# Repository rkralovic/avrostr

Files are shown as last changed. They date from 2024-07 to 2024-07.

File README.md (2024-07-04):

# AVR-OSTR

This project is an implementation of a turtle robot based on AVR microcontroller.

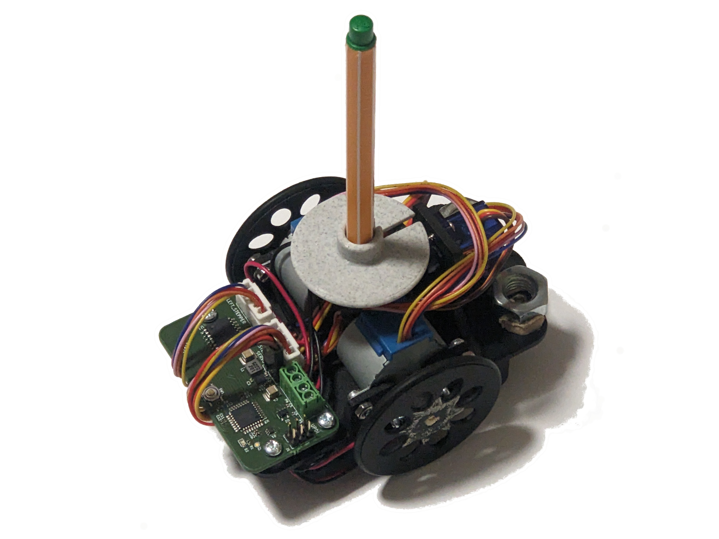
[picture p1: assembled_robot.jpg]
assembled robot


## Mechanical design

The hardware design is based on [https://www.instructables.com/OSTR/](https://www.instructables.com/OSTR/).

Mechanical parts are designed using [OpenSCAD](https://openscad.org). Running
`make` in the `mechanical` directory builds STL files suitable for 3d-printing.
The design has the following parts:

* `Chassis.scad` is the main chassis structure.
* `Caster.scad` holds a support bearing ball.
* `PenCollar.scad` holds the pen.
* `Wheel.scad` is the wheel. You need to print 2 of them

The following extra parts are needed for assembly:

* Bearing ball with diameter approx 15.875mm.
* 2x o-ring 42mm x 3mm used as tires. It is important that it fits tightly to the wheels.
* 2x battery holder for 2 AA batteries (e.g. 12BHC321A-GR).
* M3 nuts and screws (for battery holders and stepper motors).
* DIN7981 screws to fix the wheels and PCB
  ([example](https://www.conrad.ch/de/p/toolcraft-din7981-c-h-2-9c4-5-linsenblechschrauben-2-9-mm-4-5-mm-kreuzschlitz-phillips-din-7981-stahl-verzinkt-1-st-889176.html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)).
* (optional) Two large nuts that can be glued to the back of the chassis for better stability.

## Electronic design

Schematics and PCB layout are provided as a Kicad project in this directory.
Component list is summarized in `bom.csv`.

## Firmware

Source of the firmware, which runs on the AVR microcontroller of the robot, is
in the directory `fw`. You need reasonable new avr-g++ in order to compile the
firmware, which uses C++20. Development was done using avr-g++ 11.2.0.

The AVR firmware can be flashed using avrdude and an UPDI-capable programmer by
running `make write`.

A smoke test is in `fw/test`. It uses simavr library to simulate the AVR code.

Note: To compile the firmware, you need to first generate the input data, see
the next section for details. Beyond that, the tests depend on simavr, gmock,
and gtest libraries.

## Image data

The image data for the robot are prepared using a tool in `gendata` directory.
Source images are in `gendata/input` in svg file format. The tool depend on
absl, cairo, xcb, cairo-pdf, and xcb-iccm libraries.

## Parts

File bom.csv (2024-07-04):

Part number | Quantity | Designators | Footprint | Value
81-GRM155R61A106ME1D | 2 | C1,C3 | Capacitor_SMD:C_0402_1005Metric | 10u
81-GRM32ER61A107ME0K | 2 | C2,C4 | riso:C_1210_3225Metric | 100u
81-GRM155R61H105ME5D | 5 | C5,C6,C7,C9,C11 | Capacitor_SMD:C_0402_1005Metric | 1u
81-GRM155R71H104KE4D | 4 | C8,C10,C12,C14 | Capacitor_SMD:C_0402_1005Metric | 100n
GCM188R71H224KA64 | 1 | C13 | Capacitor_SMD:C_0603_1608Metric | 220n
241-BAT54BRWR100001 | 1 | D1 | Package_TO_SOT_SMD:SOT-363_SC-70-6 | BAT54BRW
710-150060RS75000 | 2 | D2,D3 | LED_SMD:LED_0603_1608Metric | RED
649-78511-203HLF | 1 | J1 | Connector_PinHeader_2.54mm:PinHeader_2x03_P2.54mm_Vertical | UPDI
XFL4020-102MEC | 1 | L1 | Inductor_SMD:L_Coilcraft_XxL4020 | 1u
651-1984617 | 2 | P5,P6 | TerminalBlock_Phoenix:TerminalBlock_Phoenix_PT-1,5-2-3.5-H_1x02_P3.50mm_Horizontal | BATT1
538-22-28-9034 | 1 | P7 | library:Pin_Header_Straight_1x03 | SERVO
603-RC0402FR-13510RL | 2 | R1,R3 | Resistor_SMD:R_0402_1005Metric | 510
603-AC0402FR-071KL | 1 | R2 | Resistor_SMD:R_0402_1005Metric | 1K
RC0402FR-07604KL | 1 | R4 | Resistor_SMD:R_0402_1005Metric | 600k
791-WR04X1003FTL | 1 | R6 | Resistor_SMD:R_0402_1005Metric | 100k
611-PTS526SM15SMTR2L | 1 | SW1 | riso:SW4-SMD-5.2X5.2X1.5MM | SMD-BUTTON_4P-5.2X5.2X1.5MM-SKQGADE010_
757-TCR1HF33BLMCT | 1 | U2 | Package_TO_SOT_SMD:SOT-23-5 | TCR1HF33
494-AVR64DD32-I/PT | 1 | U3 | Package_QFP:TQFP-32_7x7mm_P0.8mm | AVR64DD32-I/PT
595-TPS630702RNMR | 1 | U4 | riso:VQFN-15-TPS63070 | TPS63070
932-MIKROE-1530 | 2 | P3,P4 | library:JST_B5B-XH-A | LEFT_STEPPER
12BHC321A-GR | 2 | P5,P6 | TerminalBlock_Phoenix:TerminalBlock_Phoenix_PT-1,5-2-3.5-H_1x02_P3.50mm_Horizontal | BATT1
485-169 | 1 | P7 | library:Pin_Header_Straight_1x03 | SERVO
4518-ULN2803ACT-ND | 1 | U1 | Package_SO:SOP-18_7x12.5mm_P1.27mm | ULN2803

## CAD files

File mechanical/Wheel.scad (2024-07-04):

wheelDiameter = 47.5;  // not including the gasket
gasketDiameter = 3;
innerWidth = 2.0;
outerWidth = max(gasketDiameter + 1, innerWidth);

hubDiameter = 11.5;
hubHeight = 9;
hubRounding = 1;
hubCutWidth = 3.25;

// spokeDiameter = (wheelDiameter / 2 - 6.5) - 9;
spokeDiameter = ((wheelDiameter - hubDiameter) / 2 - hubRounding - outerWidth) * 0.85;
spokeAspectRatio = 0.75;
numSpokes = 8;

// pilot hole for M3 self-tapping screw in hub 
drillHoleDiameter1 = 2.5;
drillHoleDiameter2 = 2.5;

$fa = 3;
$fs = 0.3;
//$fn = 20;

module toroid(r1, r2) {
  rotate_extrude()
    translate([r2, 0, 0]) circle(r = r1);
}

module simpleCylinder(h, r) {
  cylinder(h, r, r, center = false);
}

module basicWheel() {
  difference() {
    simpleCylinder(outerWidth, wheelDiameter / 2);
    translate([0, 0, outerWidth / 2])
      toroid(gasketDiameter / 2, wheelDiameter / 2);

    minkowski() {
      translate([0, 0, outerWidth])
        simpleCylinder(outerWidth, wheelDiameter / 2 - outerWidth);
      sphere(outerWidth - innerWidth);
    }
  }
}

module spoke() {
  scale([1, spokeAspectRatio, 1])
  difference() {
    simpleCylinder(innerWidth + 1, spokeDiameter / 2);
    translate([0, 0, innerWidth / 2])
      toroid(innerWidth / 2, spokeDiameter / 2);
  }
}

module hub() {
  union() {
    minkowski() {
      translate([0, 0, hubRounding])
        simpleCylinder(hubHeight - 2 * hubRounding, (hubDiameter / 2) - hubRounding);
      sphere(hubRounding);
    };

    // bottom rounding
    difference() {
      translate([0, 0, innerWidth])
        simpleCylinder(hubRounding, hubDiameter / 2 + hubRounding);
      translate([0, 0, innerWidth + hubRounding])
        toroid(hubRounding, hubDiameter / 2 + hubRounding);
    }
  }
}

module Wheel() {
  union() {
    difference() {
      union() {
        basicWheel();
        hub();
      }

      // Drill spokes
      for (i = [0:numSpokes])
        rotate( i * 360 / numSpokes, [0, 0, 1])
          translate([-(hubDiameter / 2 + hubRounding + wheelDiameter / 2 - outerWidth) / 2, 0, 0])
            spoke();

      // Drill axis
      translate([0, 0, -1])
        intersection() {
          R = 2.75;
          simpleCylinder(hubHeight + 2, R);
          cube([hubCutWidth, 2 * R, 2 * hubHeight + 3], center = true);
        };

      // Drill Screw hole
      #for (i = [-1, 1])
        translate([i * (hubDiameter / 4 + hubCutWidth /4), 0, 6]) 
        rotate([0, 90, 0])
        rotate([90*(i + 1), 0, 0])
          cylinder((hubDiameter - hubCutWidth)/ 2 + 0.01, drillHoleDiameter1 / 2, drillHoleDiameter2 / 2, center = true);
    }
    // screw
    %translate([1.62, 0, 6]) rotate([0, 90, 0])
    union() {
      screwHeight = 4.8; // 4.5 is better, but ~6 is what I have and acceptable, too
      cylinder(h = screwHeight, d = 2.9);
      difference() {
        translate([0, 0, screwHeight])
          sphere(d = 5.6);
        translate([0, 0, screwHeight/2])
          cube([6, 6, screwHeight], center=true);
      }
    }
  }
}

Wheel();

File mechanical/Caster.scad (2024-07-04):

// Original: http://www.thingiverse.com/thing:8959/
// Marble Caster by HipsterLogic
// License: https://creativecommons.org/licenses/by-sa/3.0/

// Modified by 648.ken@gmail.com
// MakersBox.blogspot.com

// Added tapper the top lip to keep it from snagging on things.
// Added recess for screw heads if baseThickness > 3mm
// Added pedistal base so you can adjust platform hieght.

// Modified by Richard Kralovic

deckHeight = 18.5;    // from chassis bottom to ground, (must be at lease ballDiameter)
ballDiameter = 15.875;    // 7/16" ball bearing = 12.25mm, WAS 16.5  16mm = 5/8" ball bearing
ballTolerance = 0.25 + 0.25;  // play between ball and surface
wallThickness = 2.5;  // was 2.5
gapWidth = ballDiameter / 3;
baseThickness = 2.5; // was 3

pedistalWidth = ballDiameter + wallThickness * 2 + ballTolerance * 2;

baseWidth = 30; // distance between mounting holes

M3holeDia = 3.5;
M3nutDia = 6.5;

baseHeight = deckHeight - ballDiameter / 2 + ballTolerance;

module mainShape() {
  // mounting cross-piece
  translate([-baseWidth/2, -wallThickness - M3holeDia / 2, 0]) 
    cube([baseWidth, wallThickness * 2 + M3holeDia, baseThickness]);

  // bolt ends
  translate([baseWidth / 2, 0, 0]) 
    cylinder(baseThickness, M3holeDia / 2 + wallThickness, M3holeDia / 2 + wallThickness, $fn=40);
  translate([-baseWidth / 2, 0, 0]) 
    cylinder(baseThickness, M3holeDia / 2 + wallThickness, M3holeDia / 2 + wallThickness, $fn=40);


  // main cylindrical body
  translate([0, 0, 0])
    cylinder(baseHeight, pedistalWidth / 2, pedistalWidth / 2, $fn=90);

  difference(){
    // tapper shere at top
    translate([0, 0, baseHeight])
      sphere(r = pedistalWidth / 2, $fn=90);

    // shave the top flat
    R = ballDiameter / 2;
    insertRestraint = 0.5;        
    shaveHeight = sqrt((R+ballTolerance)^2 - (R - insertRestraint)^2);
    echo(shaveHeight);
    translate([0, 0, baseHeight + shaveHeight])
      cylinder(25, 25, 25, $fn=90);
  }
}

module cutout() {
  // ball hole
  translate([0, 0, baseHeight]) 
    sphere(ballDiameter / 2 + ballTolerance, $fn=90);
      
  for (r = [0:90:90]) rotate([0, 0, 45 + r]) {
    // slot to remove ball
    slotOffset = ballDiameter / 2.5;  // distance below baseHeight to cut slot
    if (baseHeight - slotOffset > baseThickness) {
      translate([-gapWidth / 2, -baseWidth / 2, baseHeight - slotOffset]) 
        cube([gapWidth, baseWidth, ballDiameter]);
    } else { // don't cut into base
      translate([-gapWidth / 2, -baseWidth / 2, baseThickness]) 
       cube([gapWidth, baseWidth, ballDiameter]);        
    }
  }
}

module mountingHoles(){
  // m3 holes
  for (i = [-1, 1]) translate([ i * baseWidth / 2, 0, -1])
    cylinder(baseThickness + 2, M3holeDia / 2, M3holeDia / 2, $fn=30);
}

module Caster() {
  rotate([0, 0, 90])
  difference() {
    mainShape();
    cutout();
    mountingHoles();
  }

  // show ball
  %translate([0, 0, baseHeight - ballTolerance]) 
    sphere(ballDiameter / 2, $fn=50);
}

Caster();

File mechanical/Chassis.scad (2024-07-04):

//$fa = 3;
//$fs = 0.3;
$fn = 50;

// Wheel diameter: 47.5 + 3 (gasket, see Wheel.scad) = 50.5
// Distance ground - shaft = 25.25
// Distance ground - bottom of chassis (Caster.scad) = 18.5
// Distance bottom of chassis - shaft = 6.75

wallThickness = 2.5;

baseThickness = wallThickness;
shaftPosition = 6.75;

module roundedCubeXYZR(xdim ,ydim ,zdim, rdim){
  hull() { // https://youtu.be/gKOkJWiTgAY
    translate([rdim, rdim, 0]) cylinder(zdim, rdim, rdim);
    translate([xdim-rdim, rdim, 0]) cylinder(zdim, rdim, rdim);
    translate([rdim, ydim-rdim, 0]) cylinder(zdim, rdim, rdim);
    translate([xdim-rdim, ydim-rdim, 0]) cylinder(zdim, rdim, rdim);
  }
}

// Interface more compatible with cube()
module roundedCube(dims, radius=2, center=false) {
  xdim = dims[0];
  ydim = dims[1];
  zdim = dims[2];
  if (center) {
    translate([-xdim  / 2, -ydim / 2, -zdim / 2])
      roundedCubeXYZR(xdim, ydim, zdim, radius);
  } else {
    roundedCubeXYZR(xdim, ydim, zdim, radius);
  }
}

module ellipsoidFillet(dims, h0, full = true) {
  module ell() {
    translate([0, 0, dims[2] / 2]) scale([1, 1, 2 * (dims[2] - h0) / dims[0]]) rotate([90, 0, 0])
      cylinder(h = dims[1] + 0.1, d = dims[0], center = true);
  }
  translate([0, 0, dims[2] / 2])
  difference() {
    cube(dims, center = true);
    if (full) {
      ell();
    } else {
      translate([-dims[0] / 2, 0, 0]) scale([2, 1, 1]) ell();
    }
  }
}

M3holeDia = 3.6;
M3nutDia = 6.5;

stepperBlockH = 17;  // distance from center to the top of the rectangular block
stepperBlockW = 14.6;
stepperBulkThickness = wallThickness + 1;

stepperShaftRadius = 5;
stepperShaftOffset = 8;
stepperDiameter = 28;
stepperTabWidth = 7;
stepperTolerance = 0.6;
module Stepper() {
  thickness = 3;

  tol= stepperTolerance;

  h1 = 19;  // body thickness, minimum 19
  h2 = 10;  // arbitrary, to have long enough drill holes
  blockH = stepperBlockH;
  blockW = stepperBlockW;
  d = stepperDiameter;
  screw_distance = 35;
  tab_width = stepperTabWidth;
  shaft_offset = stepperShaftOffset;
  shaft_radius = stepperShaftRadius;

  union() {
    rotate(-90, [0, 0, 1])
    rotate(90, [1, 0, 0])
    translate([0, shaft_offset, - h1 / 2 - tol]) {
      cylinder(h = h1 + 2 * tol, r = d / 2 + tol, center=true);  // stepper body

      for (i = [-1, 1])
        translate([i * screw_distance / 2, 0, 0]) {
          translate([0, 0, -thickness +h1 / 2 - tol])
          cylinder(h = thickness + 2*tol, r = tab_width / 2 + tol, center=false);
          translate([0, 0, -thickness +h1/2])
            cylinder(h = thickness + h2, d = M3holeDia, center=false);
        }

      translate([0, 0, h1 / 2 + tol - thickness / 2])
        cube([screw_distance, tab_width + 2*tol, thickness], center=true);

      // Not part of the motor body, but useful to keep too thin areas left
      translate([0, d/4, -thickness /2 + h1/2])
      cube([screw_distance + tab_width + 2*tol, d / 2, thickness + 2 * tol], center=true);

      // Shaft
      translate([0, -shaft_offset, h2 / 2])
        cylinder(h = h1 + h2, r = shaft_radius + tol, center=true);

        translate([0, blockH / 2, 0])
          cube([blockW + 2 * tol, blockH + 2 * tol, h1 + 2 * tol], center=true);

    }

    // Not part of the motor body, but useful to keep too thin areas left
    cutout = d * 0.25;
    translate([0, -cutout / 2, shaft_offset - d/2 - baseThickness])
      cube([h1 + 2*tol, cutout, d + 2*tol ]);
  }
}

stepperBulkW = 43;
stepperBulkH = stepperShaftOffset + shaftPosition + stepperTabWidth / 2;//19.5

module StepperBulk() {
  bulkW = stepperBulkW;
  bulkH = stepperBulkH;
  r = 2;
  bulkThickness = stepperBulkThickness;

  union() {
    translate([-(bulkW) / 2, 0, 0])
      rotate([90, 0, 0])
        union() {
          cube([bulkW, shaftPosition, bulkThickness]);
          for (i = [0, 2])
            translate([i * (bulkW / 2 + stepperShaftRadius + stepperTolerance) / 2, 0, 0])
              roundedCube([bulkW / 2 - stepperShaftRadius - stepperTolerance, bulkH, bulkThickness], r);
        }

      r2 = 5;
      translate([0, -r2/2 - bulkThickness, r2/2 + baseThickness ])
      difference() {
        filletW = bulkW - 2 * r2;
        union () {
          cube([filletW, r2, r2], center=true);
          for (i = [-1, 1])
          translate([i * filletW / 2, r2/2, -r2/2])
          intersection() {
            sphere(r2);
            translate([(i - 1) / 2 *r2, -r2, 0]) cube([r2, r2, r2]);
          }
        }
        translate([0, -r2/2, r2/2]) rotate([0, 90, 0])
          cylinder(h = 2*r2 + filletW + 0.1, r = r2, center = true);
      }
  }
}

railWidth = 2.9;
railOffset = 5.8;

penDiameter = 8.8;  // Including tolerance. Maximum 9.
// Stabilo pen has 8.4mm diameter, 0.5mm tolerance
barrelDiameter = penDiameter + 2 * wallThickness;
barrelHeight = 33;  // 26

// servo bracket variables
servoOverallHeight = 34.5;  // 34.5
servoBodyHeight = 24;
servoBodyWidth = 13;
servoScrewDia = 1.5;
servoScrewOffset = 2;
servoFwdOffset = penDiameter / 2 + wallThickness + 19;   // was 14.5
servoSideOffset = 3;
servoVerticalOffset = 8;  // distance between top of holder and servo body center, was 5

batteryOffset = 20.5;
batteryShift = 0;  // -2 is needed in the original position of servo
batteryScrewDistance = 15;

module HolderBulk() {
  baseWid = 19;
  baseLen = railWidth + 2 * railOffset;
  cornerRounding = 2;

  // pen holder
  translate([0, 0, baseThickness])
  cube([baseWid, baseLen, 2 * baseThickness], center = true);

  translate([0, 0, baseThickness])
    cylinder(barrelHeight - wallThickness / 2, r1 = baseLen / 2, r2 = barrelDiameter / 2);
  translate([0, 0, baseThickness + barrelHeight - wallThickness / 2])
    toroid(wallThickness / 2, (barrelDiameter - wallThickness) / 2);

  union() {
    bracketThickness = baseThickness + 0.5;
    bracketWidth = servoBodyWidth + 4 * baseThickness;
    // servo bracket
    rotate([0, 0, 180])
    translate([-servoFwdOffset, servoSideOffset, barrelHeight - servoVerticalOffset])
    rotate([90, 0, 90])
    union() {
      difference() {
        // base
        translate([ 0, -(barrelHeight - servoVerticalOffset - servoOverallHeight / 2) / 2, bracketThickness / 2 ])
            roundedCube([bracketWidth, servoOverallHeight / 2 + barrelHeight - servoVerticalOffset,
                         bracketThickness], cornerRounding, center = true);

        // body cutout
        translate([ 0, 0, bracketThickness / 2])
            cube([servoBodyWidth, servoBodyHeight, bracketThickness + 0.5], center = true);

        // vertical screw holes
        translate([ -0.1, -servoBodyHeight / 2 - servoScrewOffset, -0.1 ])
            cylinder(bracketThickness + 0.2, servoScrewDia / 2, servoScrewDia / 2);
        translate([ 0, servoBodyHeight / 2 + servoScrewOffset, -0.10 ])
            cylinder(bracketThickness + 0.2, servoScrewDia / 2, servoScrewDia / 2);

        // space for inserting m3 nut below
        shift = bracketThickness / 2;
        translate([-servoSideOffset, -0.1 + 1 + 2.5 + 1.5 - baseThickness / 2 - barrelHeight + servoVerticalOffset, shift])
          intersection() {
            roundedCube([5.7, 1 + 2.5 + 1.5 + baseThickness, bracketThickness + 0.1], radius = 1, center = true);
            // Ugly - we need to place the nut to the correct hole
            translate([0, 0, servoFwdOffset - shift - batteryOffset - batteryScrewDistance / 2]) rotate([90, 30, 0])
              cylinder(1 + 2*(baseThickness + 5), d = M3nutDia, center = true, $fn=6);
          }
      }

      // Servo body for checking
      %union() {
        mountOffset = 16 + 2.45;  // TODO: measure - 16 by datasheet, but that's probably not counting the thicnkess of the tab
        translate([0, 0, 26.9 / 2 - mountOffset])
          cube([12.6, 22.8, 26.9], center = true);
        translate([0, 22.8/4, 26.9 - mountOffset]) rotate([0, 0, 90])
          cylinder(h = 32.2 - 26.9, d = 7.3);
//        mountOffset = 16 + 2.45;  // TODO: measure - 16 by datasheet, but that's probably not counting the thicnkess of the tab
//        translate([0, 0, 26.7 / 2 - mountOffset])
//          cube([12.6, 22.8, 26.7], center = true);
//        translate([0, 22.8/4, 26.7 - mountOffset]) rotate([0, 0, 90])
//          cylinder(h = 34.5 - 26.7, d = 7);
      }
    }
    // fillets
    {
      w = chassisW / 2 - servoSideOffset - bracketWidth / 2 - stepperBulkThickness;
      translate([servoFwdOffset - bracketThickness / 2, w / 2 - chassisW / 2 + stepperBulkThickness, baseThickness])
      rotate([0, 0, 90]) 
        ellipsoidFillet([w + 0.01, bracketThickness, stepperBulkH], stepperBulkH / 3, false);
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

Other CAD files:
mechanical/PenCollar.scad

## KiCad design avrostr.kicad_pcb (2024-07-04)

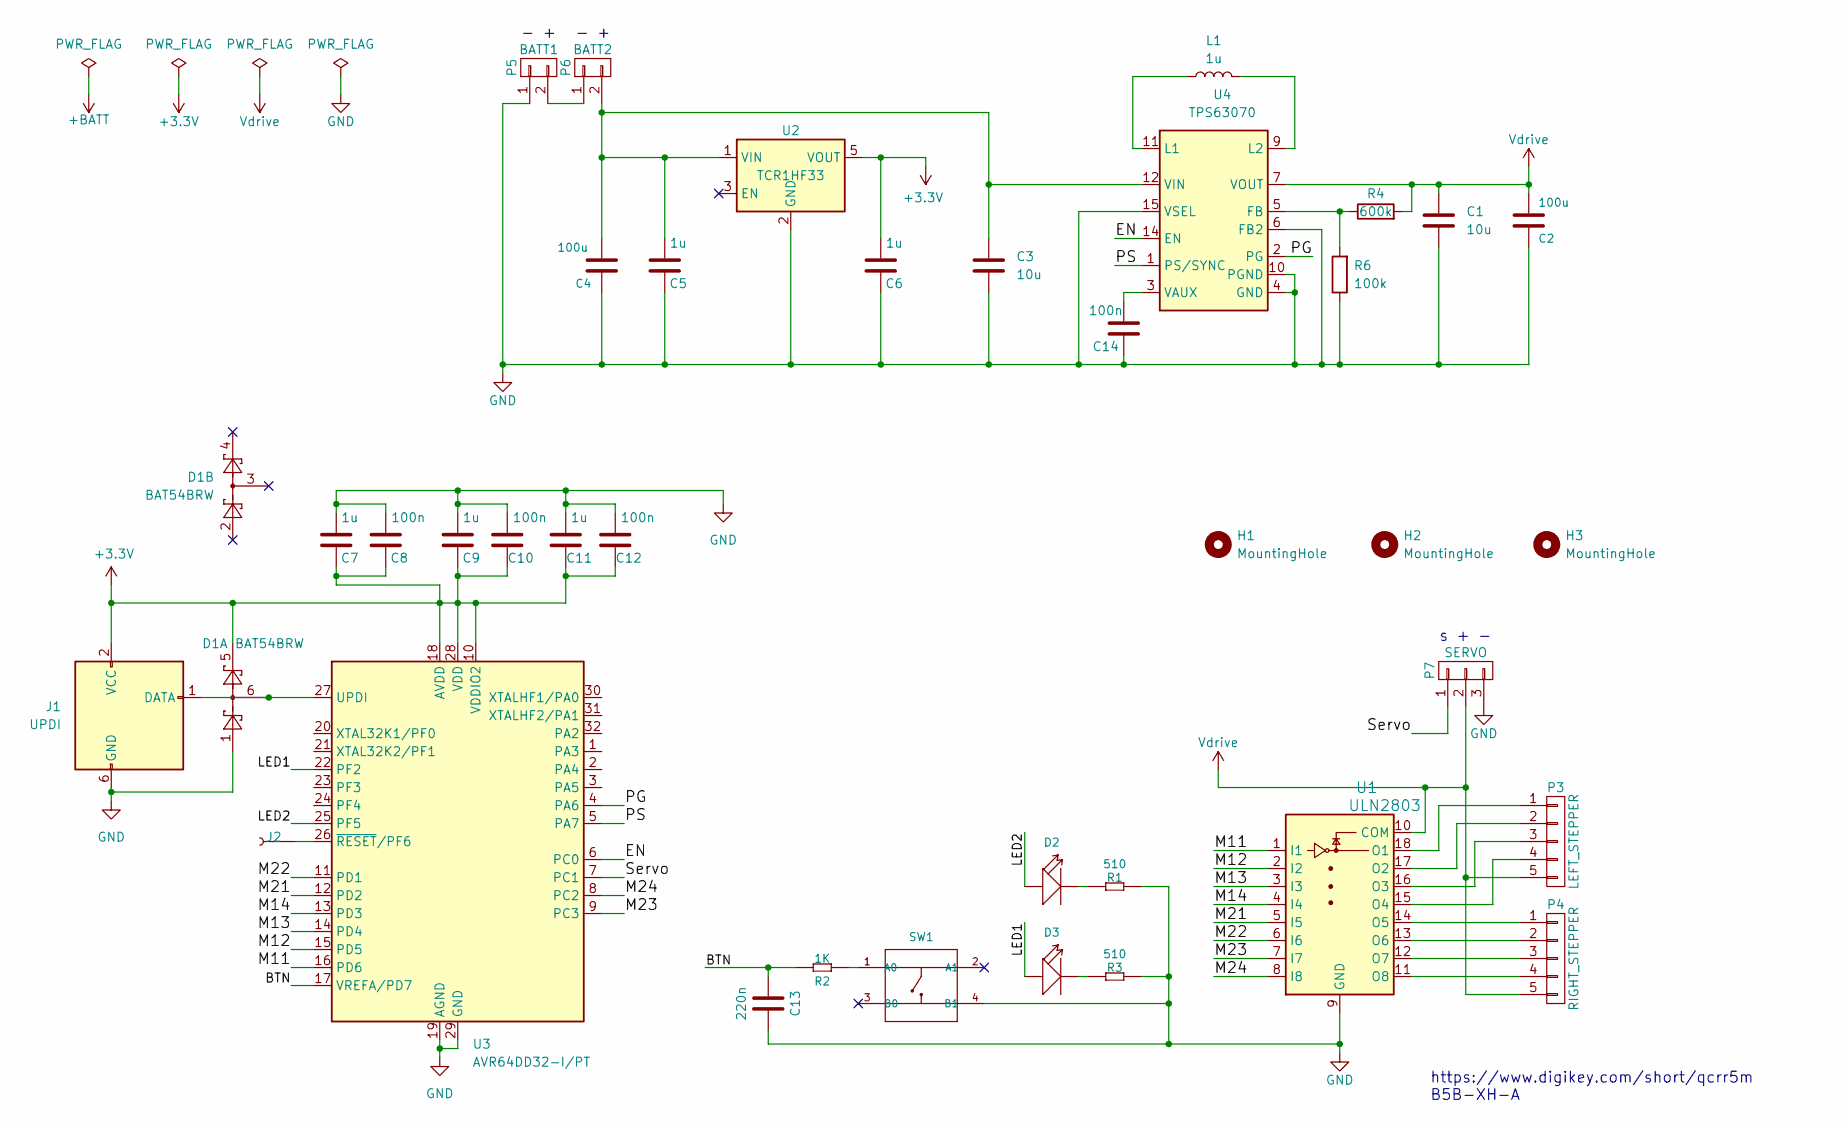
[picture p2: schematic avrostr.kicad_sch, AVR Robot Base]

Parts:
C1, C3: 10u; C_0402_1005Metric; Mouser 81-GRM155R61A106ME1D
C2, C4: 100u; C_1210_3225Metric; Mouser 81-GRM32ER61A107ME0K
C5, C6, C7, C9, C11: 1u; C_0402_1005Metric; Mouser 81-GRM155R61H105ME5D
C8, C10, C12, C14: 100n; C_0402_1005Metric; Mouser 81-GRM155R71H104KE4D
C13: 220n; C_0603_1608Metric; Mouser GCM188R71H224KA64
D1: BAT54BRW; SOT-363_SC-70-6; Mouser 241-BAT54BRWR100001
D2, D3: RED; LED_0603_1608Metric; Mouser 710-150060RS75000
H1, H2, H3: MountingHole; MountingHole_3.2mm_M3_ISO14580
J1: UPDI; PinHeader_2x03_P2.54mm_Vertical; Mouser 649-78511-203HLF
J2: Conn_01x01_Female; TestPoint_Pad_D1.0mm
L1: 1u; L_Coilcraft_XxL4020; Mouser XFL4020-102MEC
P3: LEFT_STEPPER; JST_B5B-XH-A; Digikey 455-2270-ND
P4: RIGHT_STEPPER; JST_B5B-XH-A; Digikey 455-2270-ND
P5: BATT1; TerminalBlock_Phoenix_PT-1,5-2-3.5-H_1x02_P3.50mm_Horizontal; Mouser 651-1984617
P6: BATT2; TerminalBlock_Phoenix_PT-1,5-2-3.5-H_1x02_P3.50mm_Horizontal; Mouser 651-1984617
P7: SERVO; Pin_Header_Straight_1x03; Digikey 1849-1003-ND
R1, R3: 510; R_0402_1005Metric; Mouser 603-RC0402FR-13510RL
R2: 1K; R_0402_1005Metric; Mouser 603-AC0402FR-071KL
R4: 600k; R_0402_1005Metric; Mouser RC0402FR-07604KL
R6: 100k; R_0402_1005Metric; Mouser 791-WR04X1003FTL
SW1: type="R" model="SMD-BUTTON_4P-5.2X5.2X1.5MM-SKQGA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; SW4-SMD-5.2X5.2X1.5MM; MPN SKQGADE010; LCSC C318889
U1: ULN2803; SOP-18_7x12.5mm_P1.27mm; Digikey 4518-ULN2803ACT-ND
U2: TCR1HF33; SOT-23-5; Mouser 757-TCR1HF33BLMCT
U3: AVR64DD32-I/PT; TQFP-32_7x7mm_P0.8mm; Digikey 150-AVR64DD32-I/PT-ND
U4: TPS63070; VQFN-15-TPS63070; Mouser 595-TPS630702RNMR

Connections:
+3.3V: C6.2, C7.1, C8.2, C9.1, C10.2, C11.1, C12.2, D1.5, J1.2 (VCC), U2.5 (VOUT), U3.10 (VDDIO2), U3.18 (AVDD), U3.28 (VDD)
/BTN: C13.1, R2.1, U3.17 (VREFA/PD7)
/EN: U3.6 (PC0), U4.14 (EN)
/LED1: D3.1 (+), U3.22 (PF2)
/LED2: D2.1 (+), U3.25 (PF5)
/M11: U1.1 (I1), U3.16 (PD6)
/M12: U1.2 (I2), U3.15 (PD5)
/M13: U1.3 (I3), U3.14 (PD4)
/M14: U1.4 (I4), U3.13 (PD3)
/M21: U1.5 (I5), U3.12 (PD2)
/M22: U1.6 (I6), U3.11 (PD1)
/M23: U1.7 (I7), U3.9 (PC3)
/M24: U1.8 (I8), U3.8 (PC2)
/PG: U3.4 (PA6), U4.2 (PG)
/PS: U3.5 (PA7), U4.1 (PS/SYNC)
/Servo: P7.1, U3.7 (PC1)
GND: C1.2, C2.2, C3.2, C4.2, C5.1, C6.1, C7.2, C8.1, C9.2, C10.1, C11.2, C12.1, C13.2, C14.2, D1.1, J1.6 (GND), P5.1, P7.3, R1.2, R3.2, R6.1, SW1.4 (B1), U1.9 (GND), U2.2 (GND), U3.19 (AGND), U3.29 (GND), U4.4 (GND), U4.6 (FB2), U4.10 (PGND), U4.15 (VSEL)
unnamed: C14.1, U4.3 (VAUX)
unnamed: D1.6, J1.1 (DATA), U3.27 (UPDI)
unnamed: D2.2 (-), R1.1
unnamed: D3.2 (-), R3.1
unnamed: J2.1, U3.26 (~RESET/PF6)
unnamed: L1.1, U4.11 (L1)
unnamed: L1.2, U4.9 (L2)
unnamed: P3.1, U1.18 (O1)
unnamed: P3.2, U1.17 (O2)
unnamed: P3.3, U1.16 (O3)
unnamed: P3.4, U1.15 (O4)
unnamed: P4.1, U1.14 (O5)
unnamed: P4.2, U1.13 (O6)
unnamed: P4.3, U1.12 (O7)
unnamed: P4.4, U1.11 (O8)
unnamed: P5.2, P6.1
unnamed: R2.2, SW1.1 (A0)
unnamed: R4.1, R6.2, U4.5 (FB)
VIN: C3.1, C4.1, C5.2, P6.2, U2.1 (VIN), U4.12 (VIN), U4.12_13 (VIN), U4.13 (VIN)
Vdrive: C1.1, C2.1, P3.5, P4.5, P7.2, R4.2, U1.10 (COM), U4.7 (VOUT), U4.7_8 (VOUT), U4.8 (VOUT)

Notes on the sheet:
s + -
- +
https://www.digikey.com/short/qcrr5m B5B-XH-A

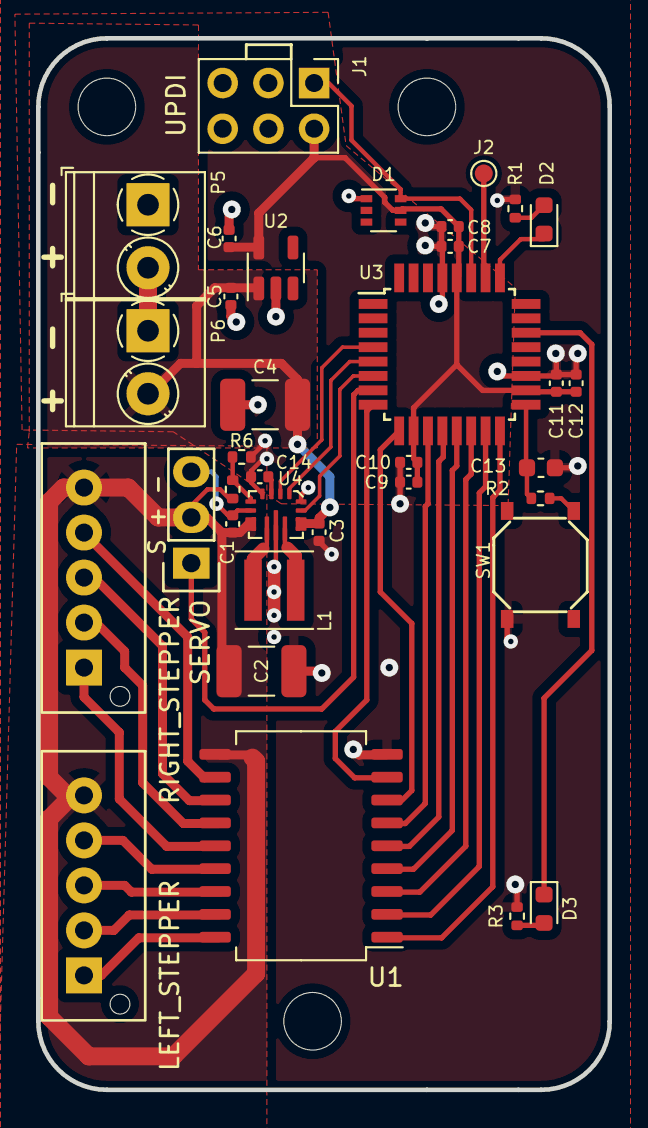
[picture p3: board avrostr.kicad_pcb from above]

Board: 2 copper layers, 31.7 x 58.4 mm, 38 parts (0 on the bottom side), 37 nets.

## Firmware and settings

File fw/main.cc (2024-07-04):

#include <avr/interrupt.h>
#include <avr/io.h>
#include <avr/sleep.h>
#include <util/delay.h>

#include <stdint.h>

#include "gpio.h"
#include "driver.h"
#include "motors.h"
#include "utils.h"
#include "stl.h"

#if ID == 1
#include "../gendata/image-a3.h"
#elif ID == 2
#include "../gendata/image-a3.h"
#endif

static_assert(F_CPU == 16000000, "Unexpected CPU frequency.");

// Image data
Image const * const kImages[] PROGMEM = {
  &kExample,
};

constexpr int8_t kNumImages = sizeof(kImages) / sizeof(const Image*);

// Calibration data in eeprom. This should be updated for each robot.
#if ID == 1
CalibrationData kCalibrationData EEMEM {
  .angle_offset = 256,
  .left_fraction = 1 << 14,
  .right_fraction = 1 << 14,
  .pen_down = 1400,
  .pen_up = 800,
};
#endif

static uint16_t kServoPeriod EEMEM = 20000;  // servo update period in us

//
// Low-level functionality
//

// MCU utils
inline void UnlockConfig() {
  CCP = CCP_IOREG_gc;
}

// Delay utils
void DelayUs(uint32_t v) {
  v = (v * (F_CPU / 1000000)) / 4;
  if (v & 0xffff) {
    _delay_loop_2(v & 0xffff);
  }
  for (uint16_t i = v >> 16; i > 0; --i) {
    _delay_loop_2(0xffff);
  }
}

void DelayMs(uint32_t v) {
  DelayUs(v * 1000);
}

// Led utils

template<typename Gpio>
void BlinkNum(Gpio& led, uint8_t num) {
  while (num-- > 0) {
    led.Set(true);
    DelayMs(200);
    led.Set(false);
    DelayMs(200);
  }
}

// Timer utils

// Measure time when cpu is running, cpu clocks.
// This class takes ownership of TCB0.
class Timer {
 public:
  static void Init() {
    TCB0.CCMP = 0xffff;  // full 16-bit period
    TCB0.CTRLA = 0x01;  // enable
  }

  static uint16_t GetTime() {
    return TCB0.CNT;
  }
};
static_assert(IsTimer<Timer>);

template <typename Timer, typename Led, typename Button>
uint8_t SelectNumber(Led* led, Button* button, uint8_t min, uint8_t max,
                     uint8_t curr) {
  auto delay = [&](bool break_value, uint32_t us) -> bool {
    uint16_t begin = Timer::GetTime();
    uint32_t ticks = us * (F_CPU / 1000000);
    while(button->Get() != break_value) {
      uint16_t end = Timer::GetTime();
      uint16_t delta = end - begin;
      if (delta > ticks) return false;
      ticks -= delta;
      begin = end;
    }
    return true;
  };

  auto blink = [&](uint8_t num) -> bool {
    for (uint8_t i = 0; i < num; ++i) {
      led->Set(true);
      if (delay(false, 200000)) {
        led->Set(false);
        return true;
      }
      led->Set(false);
      if (delay(false, 200000)) return true;
    }
    if (delay(false, 1000000)) return true;
    return false;
  };

  uint8_t retries = 5;
  while(retries > 0) {
    if (blink(curr)) {
      if (delay(true, 2000000)) {
        curr += 1;
        if (curr > max) curr = min;
        continue;
      } else {
        return curr;
      }
    }
    retries--;
  }
  return max + 1;
}

// High-current voltage regulator
// PG: gpio for power good pin
// PS: gpio for PS/SYNC pin
// EN: gpio for enable pin
template <typename PG, typename PS, typename EN>
class Power {
 public:
  Power(PG pg, PS ps, EN en)
      : pg_(std::move(pg)), ps_(std::move(ps)), en_(std::move(en)) {}

  void Init() {
    en_.ConfigureOutput();
    en_.Set(false);
    ps_.ConfigureOutput();
    ps_.Set(true);
    pg_.ConfigureInput();
    pg_.SetPullup(false);
    pg_.EnableDigitalInput(BothEdges);
    power_good_ = true;
  }

  void On() {
    pg_.SetPullup(true);
    en_.Set(true);
    // Wait until power is on.
    while(!pg_.Get());
    power_good_ = true;
  }

  void Off() {
    en_.Set(false);
    pg_.SetPullup(false);
    power_good_ = true;
  }

  void Irq() {
    power_good_ = pg_.Get();
  }

  bool Ok() const {
    return power_good_;
  }

 private:
  [[no_unique_address]] PG pg_;
  [[no_unique_address]] PS ps_;
  [[no_unique_address]] EN en_;

  volatile bool power_good_;
};

// Servo

// Global state of Servos.
// This class takes ownership of TCA0.
struct ServoState {
  uint8_t running_instances;
  uint16_t period;  // us period

  void Init() {
    running_instances = 0;
    period = eeprom_read_word(&kServoPeriod);

    static_assert(F_CPU == 1000000 || F_CPU == 16000000);
    if constexpr (F_CPU == 16000000) {
      TCA0.SINGLE.CTRLA = 0x08;  // prescaler 16x
    }
    TCA0.SINGLE.PER = period;
    TCA0.SINGLE.CTRLB = 0x03;  // singleslope mode
  }

  void On() {
    if (running_instances == 0) {
      TCA0.SINGLE.CNT = 1;
      TCA0.SINGLE.CTRLA = TCA0.SINGLE.CTRLA | 0x01;
    }
    running_instances++;
  }

  void Off() {
    running_instances--;
    if (running_instances == 0) {
      TCA0.SINGLE.CTRLA = TCA0.SINGLE.CTRLA & ~0x01;
    }
  }
};
ServoState kServoState;

// C: gpio for servo control
// Pin: convertible to integer, TCA0 output pin (CMPxEN), must correspond to C.
// PORTMUX.TCAROUTEA must be set prior to initialization.
template <typename C, typename Pin>
class Servo {
 public:
  Servo(C c, Pin pin) : c_(std::move(c)), pin_(std::move(pin)) {}

  void Init() {
    c_.ConfigureOutput();
    c_.Set(false);
    running_ = false;
  }

  void Off() {
    if (!running_) return;
    running_ = false;
    (&TCA0.SINGLE.CMP0BUF)[pin_] = 0;
    DelayUs(kServoState.period);
    TCA0.SINGLE.CTRLB = TCA0.SINGLE.CTRLB & ~(1 << (4 + pin_));
    kServoState.Off();
  }

  void Set(uint16_t pulse_us) {
    On();
    (&TCA0.SINGLE.CMP0BUF)[pin_] = pulse_us;
  }

 private:
  void On() {
    if (running_) return;
    running_ = true;
    kServoState.On();
    TCA0.SINGLE.CTRLB = TCA0.SINGLE.CTRLB | (1 << (4 + pin_));
  }

  [[no_unique_address]] C c_;
  [[no_unique_address]] Pin pin_;
  bool running_;
};
static_assert(IsServo<Servo<StaticGpio<A, 1>, StaticValue<uint8_t, 1>>>);

// Peripherals:
StaticGpio<F, 5> left_eye;
StaticGpio<F, 2> right_eye;
StaticGpio<D, 7> button;

Power power{StaticGpio<A, 6>(), StaticGpio<A, 7>(), StaticGpio<C, 0>()};

Driver driver{Timer(),
              Stepper(List(StaticGpio<D, 6>(), StaticGpio<D, 5>(),
                           StaticGpio<D, 4>(), StaticGpio<D, 3>())),
              Stepper{List(StaticGpio<D, 2>(), StaticGpio<D, 1>(),
                           StaticGpio<C, 3>(), StaticGpio<C, 2>())},
              Servo(StaticGpio<C, 1>(), StaticValue<uint8_t, 1>()),
              &kCalibrationData};

List unconnected_pins{
    StaticGpio<F, 0>(), StaticGpio<F, 1>(), StaticGpio<F, 3>(),
    StaticGpio<F, 4>(), StaticGpio<F, 0>(), StaticGpio<A, 0>(),
    StaticGpio<A, 1>(), StaticGpio<A, 2>(), StaticGpio<A, 3>(),
    StaticGpio<A, 4>(), StaticGpio<A, 5>()};

struct UnconnectedPinInitFn {
  template<typename C>
  void operator()(C& c, uint8_t) const {
    c.ConfigureInput();
    c.SetPullup(true);
  }
};

// IRQ handlers
ISR(PORTD_PORT_vect) {
  PORTD.INTFLAGS = 0xff;  // Clear interrupt flag
  sei();
}

ISR(PORTA_PORT_vect) {
  PORTA.INTFLAGS = 0xff;  // Clear interrupt flag
  sei();
  power.Irq();
}

// Board init
void BoardInit() {
  // Clock setup
  UnlockConfig();
  // Run at 16Mhz. Update F_CPU if changed.
  CLKCTRL.OSCHFCTRLA = 0x1c;

  // Brown-out detector is set up in fuses:
  // Run continuous BOD when awake and 32Hz sampled one in sleep.
  // Use 2.85V as threshold.
  // BODCFG = 0x76;

  // Initialize peripherals
  Timer::Init();
  left_eye.ConfigureOutput();
  right_eye.ConfigureOutput();
  button.ConfigureInput();
  button.SetPullup(true);
  button.EnableDigitalInput(BothEdges);
  power.Init();
  kServoState.Init();
  driver.Init();
  // Route WO1 of TCA0 to gpio C1.
  PORTMUX.TCAROUTEA = 0x02;

  // Enable pullup on unconnected pins
  unconnected_pins.ForEach(UnconnectedPinInitFn());

  sei();
}

// Sleep until button press.
void Sleep() {
  while(true) {
    cli();
    if (!button.Get()) {
      sei();
      return;
    }
    // Sleep: power down, enable
    SLPCTRL.CTRLA = 0x05;
    sei();
    sleep_cpu();
    // disable
    SLPCTRL.CTRLA = 0x00;
    DelayMs(10);
  }
}

// Low-level functionality finished.

//
// High-level logic.
//

enum Mode {
  kCalibration,
  kTest,
  kDrawImage
};

int main() {
  BoardInit();

  BlinkNum(left_eye, 2);
  uint8_t img = 1;
  Mode mode;

  while(true) {
    Sleep();

    power.On();
    right_eye.Set(true);
    while(!button.Get());
    right_eye.Set(false);
    // BlinkNum(left_eye, 3);

    uint8_t sel = SelectNumber<Timer>(&left_eye, &button, 1, kNumImages, img);
    if (sel <= kNumImages) {
      img = sel;
      mode = kDrawImage;
    } else {
      driver.Off();
      power.Off();
      continue;
    }
    BlinkNum(right_eye, sel);

    constexpr uint16_t kMaxConsecutivePowerFailures = 2;
    uint16_t power_failures = 0;

    auto interrupted = [&]() {
      if (!button.Get()) return true;
      if (power_failures > kMaxConsecutivePowerFailures) return true;
      if (!power.Ok()) {
        power_failures++;
      } else {
        power_failures = 0;
      }
      if (power_failures > kMaxConsecutivePowerFailures) return true;
      return false;
    };

    switch(mode) {
      case kCalibration:
        driver.Calibration(interrupted);
        break;
      case kTest:
        driver.TestDrive(interrupted);
        break;
      case kDrawImage:
        const Image* ptr;
        memcpy_P(&ptr, &kImages[img - 1], sizeof(const Image*));
        if (img == kNumImages) {
          img = 1;
        } else {
          img++;
        }
        driver.DrawImage(interrupted, ptr);
        break;
    }

    if (power_failures > kMaxConsecutivePowerFailures) {
      BlinkNum(right_eye, 7);
    }

    while(!button.Get());
    BlinkNum(left_eye, 3);

    driver.Off();
    power.Off();
  }

  return 0;
}

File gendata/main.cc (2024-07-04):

#include <ctype.h>
#include <math.h>
#include <stdlib.h>
#include <tinyxml2.h>

#include <numeric>
#include <sstream>
#include <string>
#include <vector>

#include "parser.h"
#include "point.h"

#define DEBUG_SHOW 1

#if DEBUG_SHOW
#include "window.h"

struct Color {
  Color(uint32_t c)
      : r{(double)((c & 0xff0000) >> 16) / 255.0},
        g{(double)((c & 0x00ff00) >> 8) / 255.0},
        b{(double)(c & 0x0000ff) / 255.0} {}
  double r, g, b;
};

std::vector<Color> palette{0x1f78b4, 0x33a02c, 0xe31a1c,
                           0xff7f00, 0x6a3d9a, 0xb15928};

// Set color
void cairo_color(cairo_t* cr, const Color& c) {
  cairo_set_source_rgb(cr, c.r, c.g, c.b);
}

// Draw filled picture
void cairo_dot(cairo_t* cr, Point p, double r = 0.01) {
  cairo_save(cr);
  cairo_new_sub_path(cr);
  cairo_arc(cr, p.x, p.y, r, 0, 2 * M_PI);
  cairo_fill(cr);
  cairo_restore(cr);
}
#endif  // DEBUG_SHOW

struct State {
  Point p;
  double alpha = M_PI / 2.0;
  double fwd_distance = 0.0;
  bool fwd = true;
};

void UpdateState(const Point& dst, State* state, int16_t* len, int16_t* angle) {
  constexpr double kWheelDiameter = 50.5;                    // mm
  constexpr double kWheelDistance = 77.2;                    // mm
  constexpr double kStepLen = M_PI * kWheelDiameter / 4096;  // mm / step
  constexpr double kStepAngle =
      2 * M_PI / 4096 * kWheelDiameter / kWheelDistance;  // radians / step

  constexpr double kMinSteps =
      4.0 / 180.0 * M_PI /
      kStepAngle;  // never perform less than this many steps on a motor.

  Point u = dst - state->p;
  *len = static_cast<uint16_t>(u.Len() / kStepLen + 0.5);
  if (fabs(*len) < kMinSteps) {
    *len = 0;
    *angle = 0;
    return;
  }

  double a = -NormalizeAngle(u.Angle() - state->alpha);

  constexpr double kMaxDistance = 100.0;  // switch directions after 100 mm
  if ((state->fwd && state->fwd_distance > kMaxDistance) ||
      (!state->fwd && state->fwd_distance < -kMaxDistance)) {
    state->fwd = !state->fwd;
  } else if (fabs(a) > M_PI / 2) {  // if there is a good time to switch, switch earlier.
    if ((state->fwd && state->fwd_distance > kMaxDistance / 2.0) ||
        (!state->fwd && state->fwd_distance < -kMaxDistance / 2.0)) {
      state->fwd = !state->fwd;
    }
  }

  if (!state->fwd) {
    a = NormalizeAngle(a + M_PI);
    *len = -(*len);
  }

  *angle = static_cast<int16_t>(a / kStepAngle + 0.5);

  if (fabs(*angle) < kMinSteps) *angle = 0;

  state->alpha += -(*angle) * kStepAngle;

  constexpr int16_t k360 = static_cast<int16_t>(2 * M_PI / kStepAngle + 0.5);
  if (state->alpha > 4 * M_PI) {
    *angle += k360;
    state->alpha += -k360 * kStepAngle;
  } else if (state->alpha < -4 * M_PI) {
    *angle -= k360;
    state->alpha -= -k360 * kStepAngle;
  }

  state->p = state->p + Point::FromAngle(state->alpha) * ((*len) * kStepLen);
  state->fwd_distance += (*len) * kStepLen;
};

int main(int argc, char** argv) {
  if (argc < 2) {
    fprintf(stderr,
            "Usage: %s <input.svg> [-elimShort <double>] [-smooth <double>] "
            "[-join <double>] [-landscape] [-a4 | -a2 | -a1]]\n",
            argv[0]);
    return 1;
  }

  const char* nameroot = "Image";

  Parser parser(argv[1]);
  bool landscape = false;
  int paper = 3;

  for (int i = 2; i < argc; i++)
    if (!strcmp(argv[i], "-elimShort")) {
      i++;
      sscanf(argv[i], "%lf", &parser.elimShortDelta);
    } else if (!strcmp(argv[i], "-smooth")) {
      i++;
      sscanf(argv[i], "%lf", &parser.smoothDelta);
    } else if (!strcmp(argv[i], "-join")) {
      i++;
      sscanf(argv[i], "%lf", &parser.joinDelta);
    } else if (!strcmp(argv[i], "-name")) {
      i++;
      nameroot = argv[i];
    } else if (!strcmp(argv[i], "-landscape")) {
      landscape = true;
    } else if (!strcmp(argv[i], "-a4")) {
      paper = 4;
    } else if (!strcmp(argv[i], "-a2")) {
      paper = 2;
    } else if (!strcmp(argv[i], "-a1")) {
      paper = 1;
    }

  fprintf(stderr, "a%d %s\n", paper, (landscape) ? "landcsape" : "portrait");
  auto layers = parser();

  // generate raw_points
  std::vector<std::pair<Point, bool>> raw_points;

  for (auto& l : layers)
    for (auto& path : l)
      for (int i = 0; i < path.size(); i++)
        raw_points.emplace_back(path[i], i > 0);

  if (raw_points.empty()) {
    fprintf(stderr, "No points\n");
    return 1;
  }

  double minx, miny, maxx, maxy;
  maxx = minx = raw_points[0].first.x;
  maxy = miny = raw_points[0].first.y;
  for (int i = 1; i < raw_points.size(); ++i) {
    minx = std::min(minx, raw_points[i].first.x);
    miny = std::min(miny, raw_points[i].first.y);
    maxx = std::max(maxx, raw_points[i].first.x);
    maxy = std::max(maxy, raw_points[i].first.y);
  }

  Point offset{-(minx + maxx) / 2.0, -(miny + maxy) / 2.0};

  // Scale for A3 paper
  double kBorder = 0.80;
  double scale;
  if (paper == 4) {
    // Scale for A4 paper
    if (landscape)
      scale = std::min(kBorder * 297.0 / (maxx - minx),
                       kBorder * 210.0 / (maxy - miny));
    else
      scale = std::min(kBorder * 210.0 / (maxx - minx),
                       kBorder * 297.0 / (maxy - miny));
  } else if (paper == 3) {
    if (landscape)
      scale = std::min(kBorder * 420.0 / (maxx - minx),
                       kBorder * 297.0 / (maxy - miny));
    else
      scale = std::min(kBorder * 297.0 / (maxx - minx),
                       kBorder * 420.0 / (maxy - miny));
  } else if (paper == 2) {
    if (landscape)
      scale = std::min(kBorder * 840.0 / (maxx - minx),
                       kBorder * 420.0 / (maxy - miny));
    else
      scale = std::min(kBorder * 420.0 / (maxx - minx),
                       kBorder * 840.0 / (maxy - miny));
  } else if (paper == 1) {
    if (landscape)
      scale = std::min(kBorder * 1680.0 / (maxx - minx),
                       kBorder * 840.0 / (maxy - miny));
    else
      scale = std::min(kBorder * 840.0 / (maxx - minx),
                       kBorder * 1680.0 / (maxy - miny));
  }

  State s;
  printf(
      "#ifndef IMAGE_%s_H_\n"
      "#define IMAGE_%s_H_\n"
      "#include <avr/pgmspace.h>\n"
      "#include \"../fw/driver.h\"\n"
      "\n"
      "const DataPoint k%sData[] PROGMEM = {\n", nameroot, nameroot, nameroot);
  {
    std::vector<std::pair<Point, bool>> filtered_points;
    for (const auto& raw_p : raw_points) {
      uint8_t pen = raw_p.second ? 1 : 0;
      int16_t len;
      int16_t angle;
      UpdateState((raw_p.first + offset) * scale, &s, &len, &angle);
      if (len != 0 || angle != 0) {
        printf("  { %d, %d, %d },\n", len, angle, pen);
        filtered_points.push_back(raw_p);
      }
    }
    raw_points = std::move(filtered_points);
  }

  printf(
      "};\n\n"
      "const Image k%s PROGMEM = { %d, k%sData };\n\n"
      "#endif  // IMAGE_%s_H_\n",
      nameroot, raw_points.size(), nameroot, nameroot);
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

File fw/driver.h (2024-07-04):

#ifndef DRIVER_H_
#define DRIVER_H_

#include <avr/eeprom.h>
#include <avr/pgmspace.h>
#include <stdint.h>

#include "motors.h"
#include "utils.h"
#include "stl.h"

struct DataPoint {
  int16_t len;
  int16_t angle : 15;
  uint8_t pen : 1;
};
static_assert(sizeof(DataPoint) == 4);

struct Image {
  uint16_t num_points;
  const DataPoint* points;  // progmem pointer
};

struct CalibrationData {
  int16_t angle_offset;  // in steps, 8.8 fixed point
  int16_t left_fraction;  // .14 fixed point
  int16_t right_fraction;  // .14 fixed point
  uint16_t pen_down;
  uint16_t pen_up;
};

using CalibrationEepromPtr = CalibrationData*;

template <typename Timer, typename LStepper, typename RStepper, typename Servo>
requires IsTimer<Timer> && IsServo<Servo> && IsStepper<LStepper> &&
    IsStepper<RStepper>
class Driver {
 public:
  Driver(Timer, LStepper lstepper, RStepper rstepper, Servo servo,
         CalibrationEepromPtr calibration)
      : left_stepper_(std::move(lstepper)),
        right_stepper_(std::move(rstepper)),
        servo_(std::move(servo)),
        angle_fraction_(0) {
    eeprom_read_block(&calibration_, calibration, sizeof(CalibrationData));
  }

  void Init() {
    left_stepper_.Init();
    right_stepper_.Init();
    servo_.Init();
    Pen(false);
  }

  void Off() {
    left_stepper_.Off();
    right_stepper_.Off();
    servo_.Off();
  }

  void Pen(bool down) {
    servo_.Set(down ? calibration_.pen_down : calibration_.pen_up);
    pen_ = down;
    DelayUs(200000);  // 200ms
  }

  template <typename Interrupted>
  bool ForwardSteps(const Interrupted& interrupted, int16_t steps) {
    int8_t sign = 1;
    if (steps < 0) {
      steps = -steps;
      sign = -1;
    }
    return Move(interrupted, -sign * calibration_.left_fraction,
                sign * calibration_.right_fraction, steps);
  }

  template <typename Interrupted>
  bool RotateSteps(const Interrupted& interrupted, int16_t steps) {
    // Ad-hoc bias
    angle_fraction_ += calibration_.angle_offset;
    steps += angle_fraction_ / 256;
    angle_fraction_ = angle_fraction_ % 256;
    int8_t sign = 1;
    if (steps < 0) {
      steps = -steps;
      sign = -1;
    }
    bool pen = pen_;
    if (kLiftPenWhenRotating) {
      if (pen) {
        Pen(false);
      }
    }
    bool val = Move(interrupted, -sign * calibration_.left_fraction,
                    -sign * calibration_.right_fraction, steps);
    if (kLiftPenWhenRotating) {
      if (pen) {
        Pen(true);
      }
    }
    return val;
  }

  // Distance um <= 500000 (0.5m)
  template <typename Interrupted>
  bool Forward(const Interrupted& interrupted, int32_t um) {
    return ForwardSteps(interrupted, (um * 4096 + 79325) / 158650);
  }

  // TODO: save remainder of rotation.
  template <typename Interrupted>
  bool Rotate(const Interrupted& interrupted, int16_t minutes) {
    // 4096 steps per rotation
    // D = 50.5mm diameter of wheel
    // L = 77.2 distance between wheels (LB: 75.6, UB 77.6)
    // 4096 * L/D steps per rotation = 21600 minutes
    int16_t d = (static_cast<int32_t>(minutes) * 10000) / 34496;
    return RotateSteps(interrupted, d);
  }

  // `image` is a progmem pointer.
  template <typename Interrupted>
  bool DrawImage(const Interrupted& interrupted, const Image* image_ptr) {
    Image image;
    memcpy_P(&image, image_ptr, sizeof(Image));
    uint8_t pen;
    uint16_t i;
    for (i = 0; i < image.num_points; ++i) {
      DataPoint p;
      memcpy_P(&p, &image.points[i], sizeof(DataPoint));
      if (i == 0 || pen != p.pen) {
        Pen(p.pen);
        pen = p.pen;
      }
      if (!RotateSteps(interrupted, p.angle)) break;
      if (!ForwardSteps(interrupted, p.len)) break;
    }
    Pen(false);
    Off();
    return i >= image.num_points;
  }

  template <typename Interrupted>
  bool TestDrive(const Interrupted& interrupted) {
    Pen(false);

    /* Just drive forward
     */
    for (int i = 0; i < 100; ++i) {
      if (!Forward(interrupted, 300000)) return false;
    }

    Off();
    return true;
  }

  template <typename Interrupted>
  bool Calibration(const Interrupted& interrupted) {
    Pen(true);

    bool val = Forward(interrupted, 200000);
    Pen(false);
    val = val &&
        Rotate(interrupted, 180 * 60);
        Rotate(interrupted, 360 * 60) && Rotate(interrupted, 360 * 60) &&
        Rotate(interrupted, 360 * 60);
    Pen(true);
    val = val && Forward(interrupted, 200000);

    Pen(false);
    Off();
    return val;
  }

 private:
  static constexpr bool kLiftPenWhenRotating = false;

  [[no_unique_address]] LStepper left_stepper_;
  [[no_unique_address]] RStepper right_stepper_;
  [[no_unique_address]] Servo servo_;

  static int16_t FractionalMove(uint16_t s, int16_t fraction, int16_t* position,
                                uint16_t* remainder) {
    int32_t p = static_cast<int32_t>(s) * fraction + *remainder;
    *remainder = p & ((1 << 14) - 1);
    p = p >> 14;
    int16_t ret = p - *position;
    *position = p;
    return ret;
  }

  // Fractions are 14-bit fixed point.
  // Returns false if interrupted.
  template <typename Interrupted>
  bool Move(const Interrupted& interrupted, int16_t left_fraction,
            int16_t right_fraction, uint16_t d) {
    Wheel w;
    uint16_t s = 0;
    int16_t l = 0;
    int16_t r = 0;
    uint16_t start = Timer::GetTime();
    while (s < d) {
      uint16_t end = Timer::GetTime();
      bool braking = ((w.v_ / (2 * Wheel::kMaxA)) * w.v_) >> 48 >= d - s;
      s += w.Update(end - start, braking ? -Wheel::kMaxA : Wheel::kMaxA);
      start = end;

      left_stepper_.Move(FractionalMove(s, left_fraction, &l, &left_remainder_));
      right_stepper_.Move(FractionalMove(s, right_fraction, &r, &right_remainder_));

      if (interrupted()) return false;
    }
    return true;
  }

  void DelayUs(uint32_t t) {
    t *= F_CPU / 1000000;
    uint16_t begin = Timer::GetTime();
    while (true) {
      uint16_t end = Timer::GetTime();
      uint16_t delta = end - begin;
      if (delta > t) break;
      t -= delta;
      begin = end;
    }
  }

  struct Wheel {
    int64_t s_ = 0;  // steps, 48-bit fixed point
    int64_t v_ = 0;  // steps / tick, 48-bit fixed point

    static constexpr int64_t kMaxV = (750ll << 48) / F_CPU;  // 750 step/second
    static constexpr int64_t kMaxA =
        kMaxV / (F_CPU / 10);  // 0 to kMaxV in 100ms

    // Update state for `dt_ticks` with acceleration `a`. Acceleration must be
    // between -kMaxA and +kMaxA. Returns number of steps of the motor.
    int8_t Update(uint16_t dt_ticks, int64_t a) {
      int64_t v2 = v_ + a * dt_ticks;
      if (v2 > kMaxV) {
        v2 = kMaxV;
      } else if (v2 < -kMaxV) {
        v2 = -kMaxV;
      }
      s_ += (v_ + v2) * dt_ticks / 2;
      v_ = v2;
      if (s_ > 1ll << 47) {
        s_ -= 1ll << 48;
        return 1;
      } else if (s_ < -(1ll << 47)) {
        s_ += 1ll << 48;
        return -1;
      }
      return 0;
    }
  };

  bool pen_ = false;
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
